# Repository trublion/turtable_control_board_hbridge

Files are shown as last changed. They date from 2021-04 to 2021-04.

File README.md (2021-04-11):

## Description

HW control board for turntable. Controls a DC motor with a H-bridge, reads an analog audio signal envelope, dual-PCB design.

## Links (datasheets and documentation)

[IEC plug](https://www.schurter.com/en/datasheet/typ_6765.pdf)  
[Potentiometer RK09L](https://tech.alpsalpine.com/prod/e/pdf/potentiometer/rotarypotentiometers/rk09l/rk09l.pdf)  
[Neutrik combo](https://www.neutrik.com/en/product/nj3fp6c.pdf)  
[74HCT4066](https://assets.nexperia.com/documents/data-sheet/74HC_HCT4066.pdf)  
[Shunt resistors](https://www.te.com/commerce/DocumentDelivery/DDEController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)  
[BAS21 small signal diode](https://www.vishay.com/docs/85540/bas19.pdf)  
[Zener diodes](https://assets.nexperia.com/documents/data-sheet/BZX84_SER.pdf)  
[Electrolytic capacitors](https://industrial.panasonic.com/cdbs/www-data/pdf/RDE0000/ABA0000C1181.pdf)  
[LM358 comparator](https://www.ti.com/lit/ds/symlink/lm158-n.pdf)  
[LM833 operational amplifier](https://www.ti.com/lit/ds/symlink/lm833-n.pdf)  
[LM2674 DCDC controller](https://www.ti.com/lit/ds/symlink/lm2674.pdf)  
[MBRS3100T3G Schottky power diode](https://www.onsemi.com/pdf/datasheet/mbrs3100t3-d.pdf)  
[RS2 power diode](https://www.semiee.com/file/ELMX/MULTICOMP-RS2A.pdf)  
[Power inductor](https://www.bourns.com/docs/Product-Datasheets/SRR0735A.pdf)

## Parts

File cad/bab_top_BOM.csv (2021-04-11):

Source: | C:\Users\Florian\Documents\dev\trublion\bab leo maurel\v2\cad\bab_top.sch
Date: | 11/04/2021 16:08:11
Tool: | Eeschema (5.1.9)-1
Generator: | E:\dev\KiCad\bin\scripting\plugins/bom_csv_grouped_by_value.py
Component Count: | 106
Individual Components:
Item | Qty | Reference(s) | Value | LibPart | Footprint | Datasheet
 |  | C101 | 100n | Device:C | Capacitors_SMD:C_0805_HandSoldering
 |  | C102 | 100n | Device:C | Capacitors_SMD:C_0805_HandSoldering
 |  | C201 | 1u | Device:C | Capacitors_SMD:C_2220_HandSoldering
 |  | C202 | 100p | Device:C | Capacitors_SMD:C_0805_HandSoldering
 |  | C203 | 47u | Device:C | Capacitors_SMD:c_elec_6.3x5.8
 |  | C204 | 47u | Device:C | Capacitors_SMD:c_elec_6.3x5.8
 |  | C205 | 100p | Device:C | Capacitors_SMD:C_0805_HandSoldering
 |  | C206 | 47u | Device:C | Capacitors_SMD:c_elec_6.3x5.8
 |  | C207 | 6.8u | Device:C | Capacitors_SMD:c_elec_5x5.7
 |  | C208 | 100n | Device:C | Capacitors_SMD:C_0805_HandSoldering
 |  | C209 | 10u | Device:C | Capacitors_SMD:c_elec_6.3x5.8
 |  | C303 | 100u | Device:CP | Capacitors_SMD:c_elec_6.3x7.7
 |  | C304 | 100n | Device:C | Capacitors_SMD:C_0805_HandSoldering
 |  | C305 | 10n | Device:C | Capacitors_SMD:C_0805_HandSoldering
 |  | C306 | 100u | Device:CP | Capacitors_SMD:c_elec_6.3x7.7
 |  | C307 | 100n | Device:C | Capacitors_SMD:C_0805_HandSoldering
 |  | C401 | 100u | Device:CP | Capacitors_SMD:c_elec_6.3x7.7
 |  | C402 | 470p | Device:C | Capacitors_SMD:C_0805_HandSoldering
 |  | C403 | 10n | Device:C | Capacitors_SMD:C_0805_HandSoldering
 |  | C404 | 100u | Device:CP | Capacitors_SMD:c_elec_6.3x7.7
 |  | C405 | 10u | Device:CP | Capacitors_SMD:c_elec_6.3x5.8
 |  | C406 | 220n | Device:C | Capacitors_SMD:C_0805_HandSoldering
 |  | C407 | 470u | Device:CP | bab_footprint:c_elec_16x16.8
 |  | C408 | 100n | Device:C | Capacitors_SMD:C_0805_HandSoldering
 |  | C409 | 15n | Device:C | Capacitors_SMD:C_0805_HandSoldering
 |  | C410 | 15n | Device:C | Capacitors_SMD:C_0805_HandSoldering
 |  | C411 | 4.7n | Device:C | Capacitors_SMD:C_0805_HandSoldering
 |  | C412 | 100n | Device:C | Capacitors_SMD:C_0805_HandSoldering
 |  | D101 | BAS21 | bab:BAS21 | TO_SOT_Packages_SMD:SOT-23
 |  | D201 | BAS21 | bab:BAS21 | TO_SOT_Packages_SMD:SOT-23
 |  | D202 | BAS21 | bab:BAS21 | TO_SOT_Packages_SMD:SOT-23
 |  | D301 | MBRS3100T3G | Device:D_Schottky | Diodes_SMD:DO-214AB
 |  | D302 | MBRS3100T3G | Device:D_Schottky | Diodes_SMD:DO-214AB
 |  | D303 | MBRS3100T3G | Device:D_Schottky | Diodes_SMD:DO-214AB
 |  | D401 | BZX84C5V1 | bab:BZX84C5V1 | TO_SOT_Packages_SMD:SOT-23
 |  | D402 | BAS21 | bab:BAS21 | TO_SOT_Packages_SMD:SOT-23
 |  | D403 | BAS21 | bab:BAS21 | TO_SOT_Packages_SMD:SOT-23
 |  | D404 | RS2M | Device:D | bab_footprint:DO-214AA_Handsoldering
 |  | D405 | RS2M | Device:D | bab_footprint:DO-214AA_Handsoldering
 |  | D406 | BZX84C5V1 | bab:BZX84C5V1 | TO_SOT_Packages_SMD:SOT-23
 |  | K101 | XLR3 | bab_top-rescue:XLR3 | Pin_Headers:Pin_Header_Straight_1x03
 |  | K102 | XLR3 | bab_top-rescue:XLR3 | Pin_Headers:Pin_Header_Straight_1x03
 |  | L301 | 100u | bab_top-rescue:INDUCTOR | Choke_SMD:Choke_SMD_7.3x7.3_H3.5
 |  | P2 | CONN_01X02 | bab_top-rescue:CONN_01X02 | Pin_Headers:Pin_Header_Straight_1x02
 |  | P3 | CONN_01X02 | bab_top-rescue:CONN_01X02 | Pin_Headers:Pin_Header_Straight_1x02
 |  | P4 | CONN_01X02 | bab_top-rescue:CONN_01X02 | Pin_Headers:Pin_Header_Straight_1x02
 |  | P5 | CONN_01X03 | bab_top-rescue:CONN_01X03 | Pin_Headers:Pin_Header_Straight_1x03
 |  | P6 | CONN_01X03 | bab_top-rescue:CONN_01X03 | Pin_Headers:Pin_Header_Straight_1x03
 |  | P101 | CONN_01X02 | bab_top-rescue:CONN_01X02 | Connect:bornier2
 |  | P102 | CONN_01X02 | bab_top-rescue:CONN_01X02 | Connect:bornier2
 |  | P103 | Nulceo_F303K8_CONN | bab:Nulceo_F303K8_CONN | bab_footprint:Nucleo_F303K8_CONN
 |  | P104 | CONN_01X03 | bab_top-rescue:CONN_01X03 | Pin_Headers:Pin_Header_Straight_1x03
 |  | P105 | CONN_01X03 | bab_top-rescue:CONN_01X03 | Pin_Headers:Pin_Header_Straight_1x03
 |  | P106 | CONN_01X02 | bab_top-rescue:CONN_01X02 | Connect:bornier2
 |  | P107 | CONN_01X02 | bab_top-rescue:CONN_01X02 | Connect:bornier2
 |  | P108 | CONN_01X03 | bab_top-rescue:CONN_01X03 | Pin_Headers:Pin_Header_Straight_1x03
 |  | P109 | CONN_01X03 | bab_top-rescue:CONN_01X03 | Pin_Headers:Pin_Header_Straight_1x03
 |  | Q1 | DTC123Y | bab_top-rescue:DTC123Y | TO_SOT_Packages_SMD:SOT-23_Handsoldering
 |  | Q401 | DTC123Y | bab_top-rescue:DTC123Y | TO_SOT_Packages_SMD:SOT-23
 |  | Q402 | DTC123Y | bab_top-rescue:DTC123Y | TO_SOT_Packages_SMD:SOT-23
 |  | R1 | 1k | Device:R | Resistors_SMD:R_0805_HandSoldering
 |  | R2 | 1k | Device:R | Resistors_SMD:R_0805_HandSoldering
 |  | R103 | 33k | Device:R | Capacitors_SMD:C_0805_HandSoldering
 |  | R104 | 4.7k | Device:R | Capacitors_SMD:C_0805_HandSoldering
 |  | R105 | 10k | Device:R | Capacitors_SMD:C_0805_HandSoldering
 |  | R106 | 0 | Device:R | Capacitors_SMD:C_0805_HandSoldering
 |  | R201 | 1k | Device:R | Capacitors_SMD:C_0805_HandSoldering
 |  | R202 | 1M | Device:R | Capacitors_SMD:C_0805_HandSoldering
 |  | R203 | 33k | Device:R | Capacitors_SMD:C_0805_HandSoldering
 |  | R204 | 33k | Device:R | Capacitors_SMD:C_0805_HandSoldering
 |  | R205 | 1k | Device:R | Capacitors_SMD:C_0805_HandSoldering
 |  | R206 | 100 | Device:R | Capacitors_SMD:C_0805_HandSoldering
 |  | R207 | 75k | Device:R | Capacitors_SMD:C_0805_HandSoldering
 |  | R208 | 10k | Device:R | Capacitors_SMD:C_0805_HandSoldering
 |  | R209 | 33k | Device:R | Capacitors_SMD:C_0805_HandSoldering
 |  | R210 | 33k | Device:R | Capacitors_SMD:C_0805_HandSoldering
 |  | R211 | 33k | Device:R | Capacitors_SMD:C_0805_HandSoldering
 |  | R212 | 33k | Device:R | Capacitors_SMD:C_0805_HandSoldering
 |  | R213 | 33k | Device:R | Capacitors_SMD:C_0805_HandSoldering
 |  | R214 | 10k | Device:R | Capacitors_SMD:C_0805_HandSoldering
 |  | R401 | 4k7 | Device:R | Capacitors_SMD:C_0805_HandSoldering
 |  | R402 | 1k | Device:R | Capacitors_SMD:C_0805_HandSoldering
 |  | R404 | 1k | Device:R | Capacitors_SMD:C_0805_HandSoldering
 |  | R405 | 10k | Device:R | Capacitors_SMD:C_0805_HandSoldering
 |  | R406 | 0 | Device:R | Capacitors_SMD:C_0805_HandSoldering
 |  | R407 | 0 | Device:R | Capacitors_SMD:C_0805_HandSoldering
 |  | R408 | 10k | Device:R | Capacitors_SMD:C_0805_HandSoldering
 |  | R409 | 0 | Device:R | Capacitors_SMD:C_0805_HandSoldering
 |  | R410 | 0 | Device:R | Capacitors_SMD:C_0805_HandSoldering
 |  | R411 | 0 | Device:R | Capacitors_SMD:C_0805_HandSoldering
 |  | R412 | 0 | Device:R | Capacitors_SMD:C_0805_HandSoldering
 |  | R413 | 0 | Device:R | Capacitors_SMD:C_0805_HandSoldering
 |  | R414 | 24 | Device:R | bab_footprint:C_3522_HandSoldering
 |  | RV101 | 10k | bab_top-rescue:POT | Pin_Headers:Pin_Header_Straight_1x03
 |  | RV201 | 100k | bab_top-rescue:POT | Pin_Headers:Pin_Header_Straight_1x03
 |  | RV202 | 10k | bab_top-rescue:POT | Pin_Headers:Pin_Header_Straight_1x03
 |  | RV203 | 1k | bab_top-rescue:POT | Pin_Headers:Pin_Header_Straight_1x03
 |  | RV204 | 1M | bab_top-rescue:POT | Pin_Headers:Pin_Header_Straight_1x03
 |  | RV205 | 100k | bab_top-rescue:POT | Pin_Headers:Pin_Header_Straight_1x03
 |  | SW401 | SWITCH_INV | bab_top-rescue:SWITCH_INV | Pin_Headers:Pin_Header_Straight_1x03
 |  | U201 | LM833 | bab:LM833 | Housings_SOIC:SOIC-8_3.9x4.9mm_Pitch1.27mm
 |  | U202 | LM358 | bab_top-rescue:LM358-RESCUE-bab_top | Housings_SOIC:SOIC-8_3.9x4.9mm_Pitch1.27mm
 |  | U301 | LM2674 | bab:LM2674 | Housings_SOIC:SOIC-8_3.9x4.9mm_Pitch1.27mm
 |  | U401 | LM7812CT | bab_top-rescue:LM7812CT | Power_Integrations:TO-220
 |  | U402 | LM555N | bab_top-rescue:LM555N-RESCUE-bab_top | Housings_SOIC:SOIC-8_3.9x4.9mm_Pitch1.27mm
 |  | U403 | L6203 | bab:L6203 | bab_footprint:Multiwatt_11_Vertical | ~
Collated Components:
Item | Qty | Reference(s) | Value | LibPart | Footprint | Datasheet
1 | 7 | C101, C102, C208, C304, C307, C408, C412 | 100n | Device:C | Capacitors_SMD:C_0805_HandSoldering
2 | 1 | C201 | 1u | Device:C | Capacitors_SMD:C_2220_HandSoldering
3 | 2 | C202, C205 | 100p | Device:C | Capacitors_SMD:C_0805_HandSoldering
4 | 3 | C203, C204, C206 | 47u | Device:C | Capacitors_SMD:c_elec_6.3x5.8
5 | 1 | C207 | 6.8u | Device:C | Capacitors_SMD:c_elec_5x5.7
6 | 1 | C209 | 10u | Device:C | Capacitors_SMD:c_elec_6.3x5.8
7 | 4 | C303, C306, C401, C404 | 100u | Device:CP | Capacitors_SMD:c_elec_6.3x7.7
8 | 2 | C305, C403 | 10n | Device:C | Capacitors_SMD:C_0805_HandSoldering
9 | 1 | C402 | 470p | Device:C | Capacitors_SMD:C_0805_HandSoldering
10 | 1 | C405 | 10u | Device:CP | Capacitors_SMD:c_elec_6.3x5.8
11 | 1 | C406 | 220n | Device:C | Capacitors_SMD:C_0805_HandSoldering
12 | 1 | C407 | 470u | Device:CP | bab_footprint:c_elec_16x16.8
13 | 2 | C409, C410 | 15n | Device:C | Capacitors_SMD:C_0805_HandSoldering
14 | 1 | C411 | 4.7n | Device:C | Capacitors_SMD:C_0805_HandSoldering
15 | 5 | D101, D201, D202, D402, D403 | BAS21 | bab:BAS21 | TO_SOT_Packages_SMD:SOT-23
16 | 3 | D301, D302, D303 | MBRS3100T3G | Device:D_Schottky | Diodes_SMD:DO-214AB
17 | 2 | D401, D406 | BZX84C5V1 | bab:BZX84C5V1 | TO_SOT_Packages_SMD:SOT-23
18 | 2 | D404, D405 | RS2M | Device:D | bab_footprint:DO-214AA_Handsoldering
19 | 2 | K101, K102 | XLR3 | bab_top-rescue:XLR3 | Pin_Headers:Pin_Header_Straight_1x03
20 | 1 | L301 | 100u | bab_top-rescue:INDUCTOR | Choke_SMD:Choke_SMD_7.3x7.3_H3.5
21 | 3 | P2, P3, P4 | CONN_01X02 | bab_top-rescue:CONN_01X02 | Pin_Headers:Pin_Header_Straight_1x02
22 | 6 | P5, P6, P104, P105, P108, P109 | CONN_01X03 | bab_top-rescue:CONN_01X03 | Pin_Headers:Pin_Header_Straight_1x03
23 | 4 | P101, P102, P106, P107 | CONN_01X02 | bab_top-rescue:CONN_01X02 | Connect:bornier2
24 | 1 | P103 | Nulceo_F303K8_CONN | bab:Nulceo_F303K8_CONN | bab_footprint:Nucleo_F303K8_CONN
25 | 1 | Q1 | DTC123Y | bab_top-rescue:DTC123Y | TO_SOT_Packages_SMD:SOT-23_Handsoldering
26 | 2 | Q401, Q402 | DTC123Y | bab_top-rescue:DTC123Y | TO_SOT_Packages_SMD:SOT-23
27 | 2 | R1, R2 | 1k | Device:R | Resistors_SMD:R_0805_HandSoldering
28 | 8 | R103, R203, R204, R209, R210, R211, R212, R213 | 33k | Device:R | Capacitors_SMD:C_0805_HandSoldering
29 | 1 | R104 | 4.7k | Device:R | Capacitors_SMD:C_0805_HandSoldering
30 | 5 | R105, R208, R214, R405, R408 | 10k | Device:R | Capacitors_SMD:C_0805_HandSoldering
31 | 8 | R106, R406, R407, R409, R410, R411, R412, R413 | 0 | Device:R | Capacitors_SMD:C_0805_HandSoldering
32 | 4 | R201, R205, R402, R404 | 1k | Device:R | Capacitors_SMD:C_0805_HandSoldering
33 | 1 | R202 | 1M | Device:R | Capacitors_SMD:C_0805_HandSoldering
34 | 1 | R206 | 100 | Device:R | Capacitors_SMD:C_0805_HandSoldering
35 | 1 | R207 | 75k | Device:R | Capacitors_SMD:C_0805_HandSoldering
36 | 1 | R401 | 4k7 | Device:R | Capacitors_SMD:C_0805_HandSoldering
37 | 1 | R414 | 24 | Device:R | bab_footprint:C_3522_HandSoldering
38 | 2 | RV101, RV202 | 10k | bab_top-rescue:POT | Pin_Headers:Pin_Header_Straight_1x03
39 | 2 | RV201, RV205 | 100k | bab_top-rescue:POT | Pin_Headers:Pin_Header_Straight_1x03
40 | 1 | RV203 | 1k | bab_top-rescue:POT | Pin_Headers:Pin_Header_Straight_1x03
41 | 1 | RV204 | 1M | bab_top-rescue:POT | Pin_Headers:Pin_Header_Straight_1x03
42 | 1 | SW401 | SWITCH_INV | bab_top-rescue:SWITCH_INV | Pin_Headers:Pin_Header_Straight_1x03
43 | 1 | U201 | LM833 | bab:LM833 | Housings_SOIC:SOIC-8_3.9x4.9mm_Pitch1.27mm
44 | 1 | U202 | LM358 | bab_top-rescue:LM358-RESCUE-bab_top | Housings_SOIC:SOIC-8_3.9x4.9mm_Pitch1.27mm
45 | 1 | U301 | LM2674 | bab:LM2674 | Housings_SOIC:SOIC-8_3.9x4.9mm_Pitch1.27mm
46 | 1 | U401 | LM7812CT | bab_top-rescue:LM7812CT | Power_Integrations:TO-220
47 | 1 | U402 | LM555N | bab_top-rescue:LM555N-RESCUE-bab_top | Housings_SOIC:SOIC-8_3.9x4.9mm_Pitch1.27mm
48 | 1 | U403 | L6203 | bab:L6203 | bab_footprint:Multiwatt_11_Vertical | ~

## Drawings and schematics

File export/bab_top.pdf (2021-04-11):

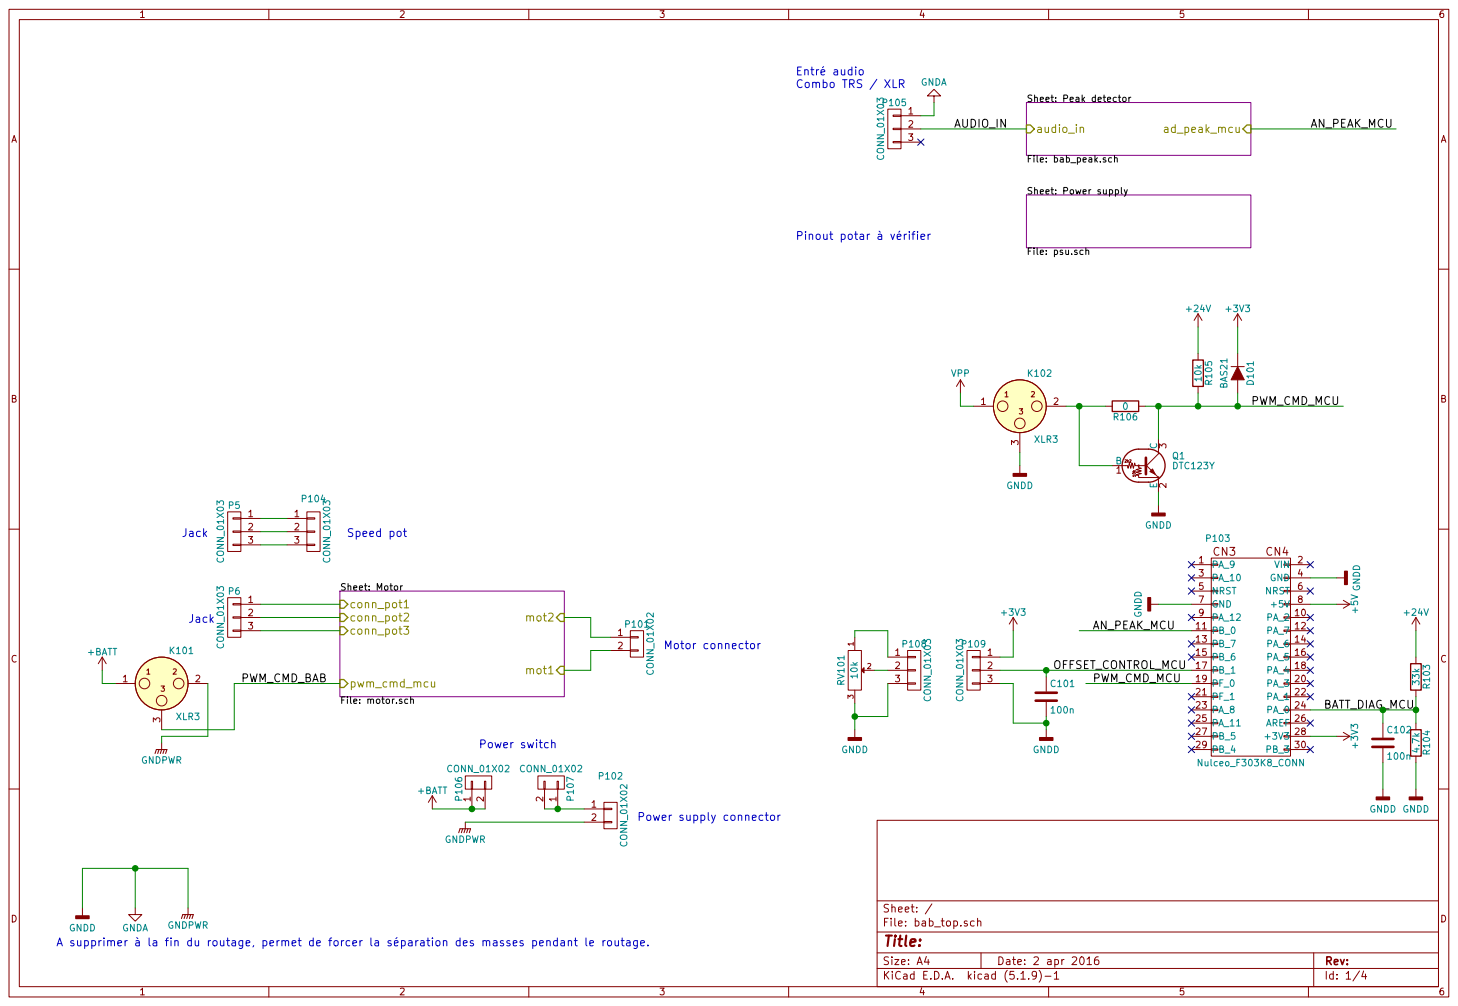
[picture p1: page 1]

File: psu.sch Sheet: Peak detector File: bab_peak.sch

File: bab_top.sch Sheet: / Sheet: Motor File: motor.sch conn_pot1

A supprimer à la fin du routage, permet de forcer la séparation des masses pendant le routage.

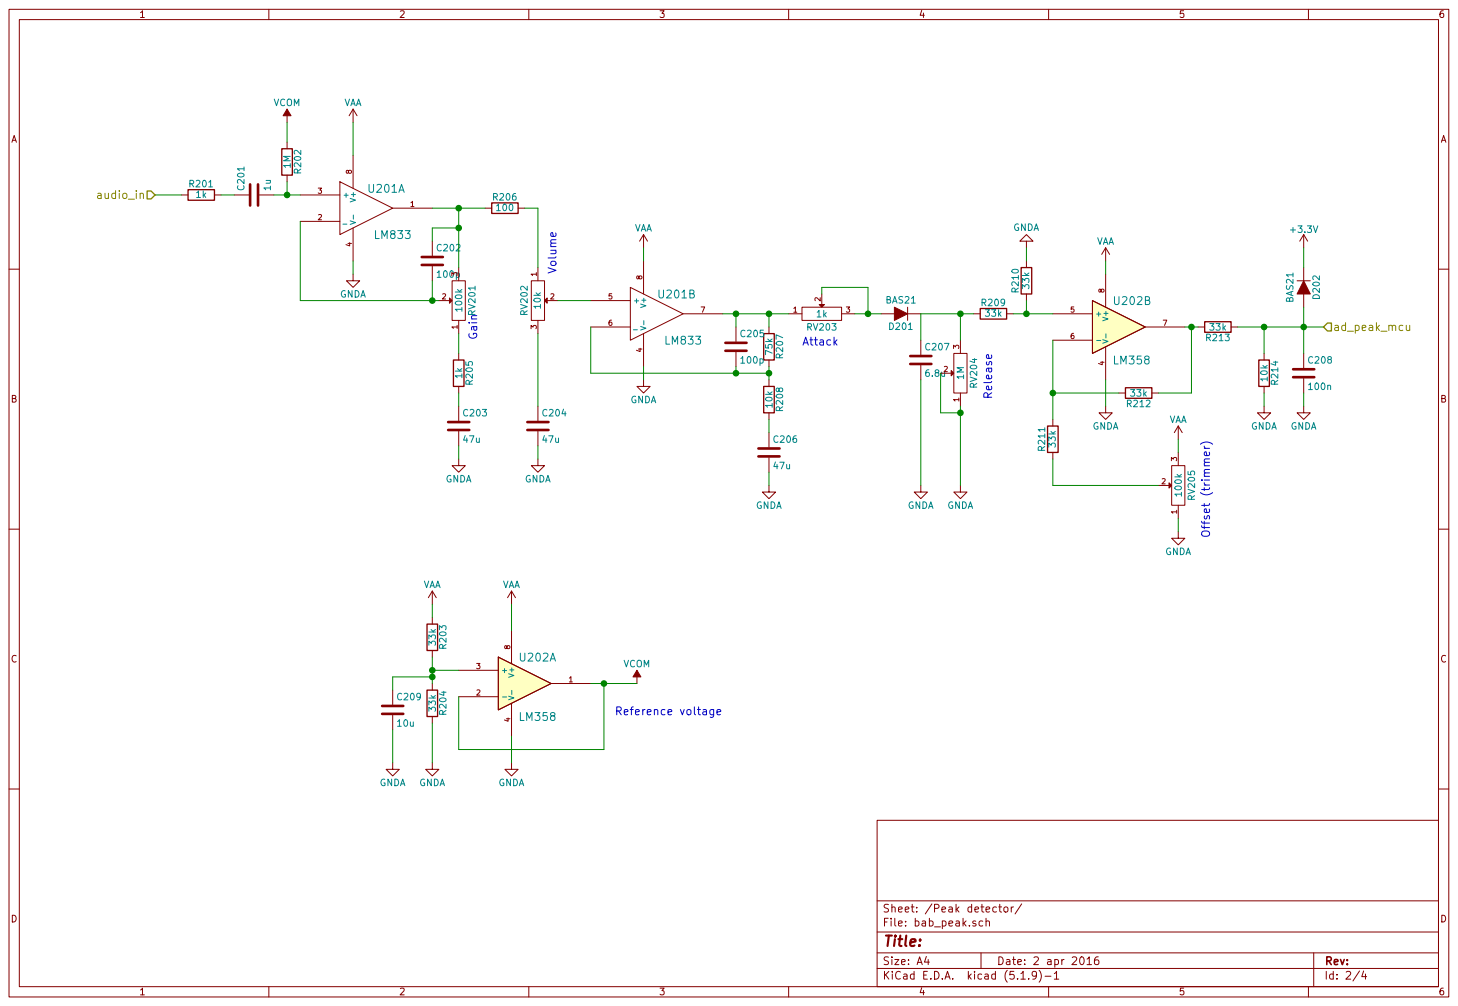
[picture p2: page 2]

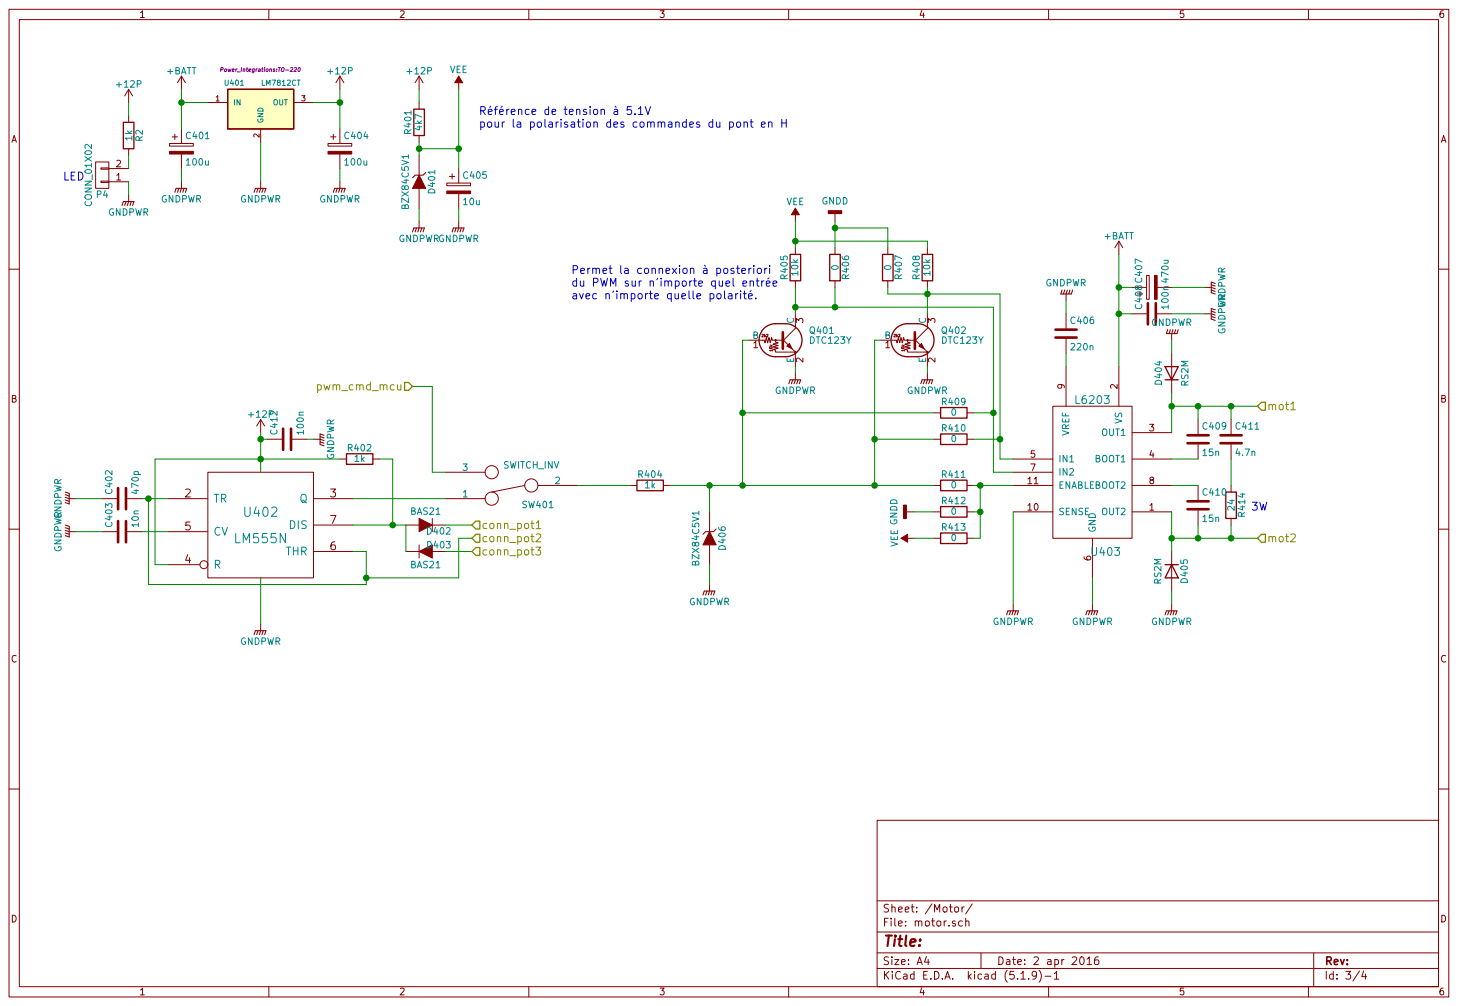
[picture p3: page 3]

Référence de tension à 5.1V
pour la polarisation des commandes du pont en H

avec n'importe quelle polarité. LED

Permet la connexion à posteriori
du PWM sur n'importe quel entrée

Id: 3/4 Title: File: motor.sch Sheet: /Motor/ GNDPWR

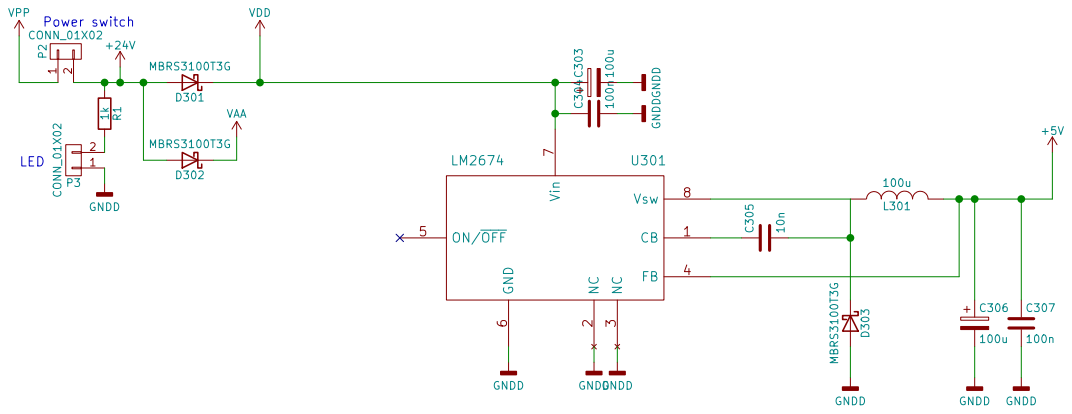
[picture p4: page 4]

3 FB 4 ON/OFF 5 GND

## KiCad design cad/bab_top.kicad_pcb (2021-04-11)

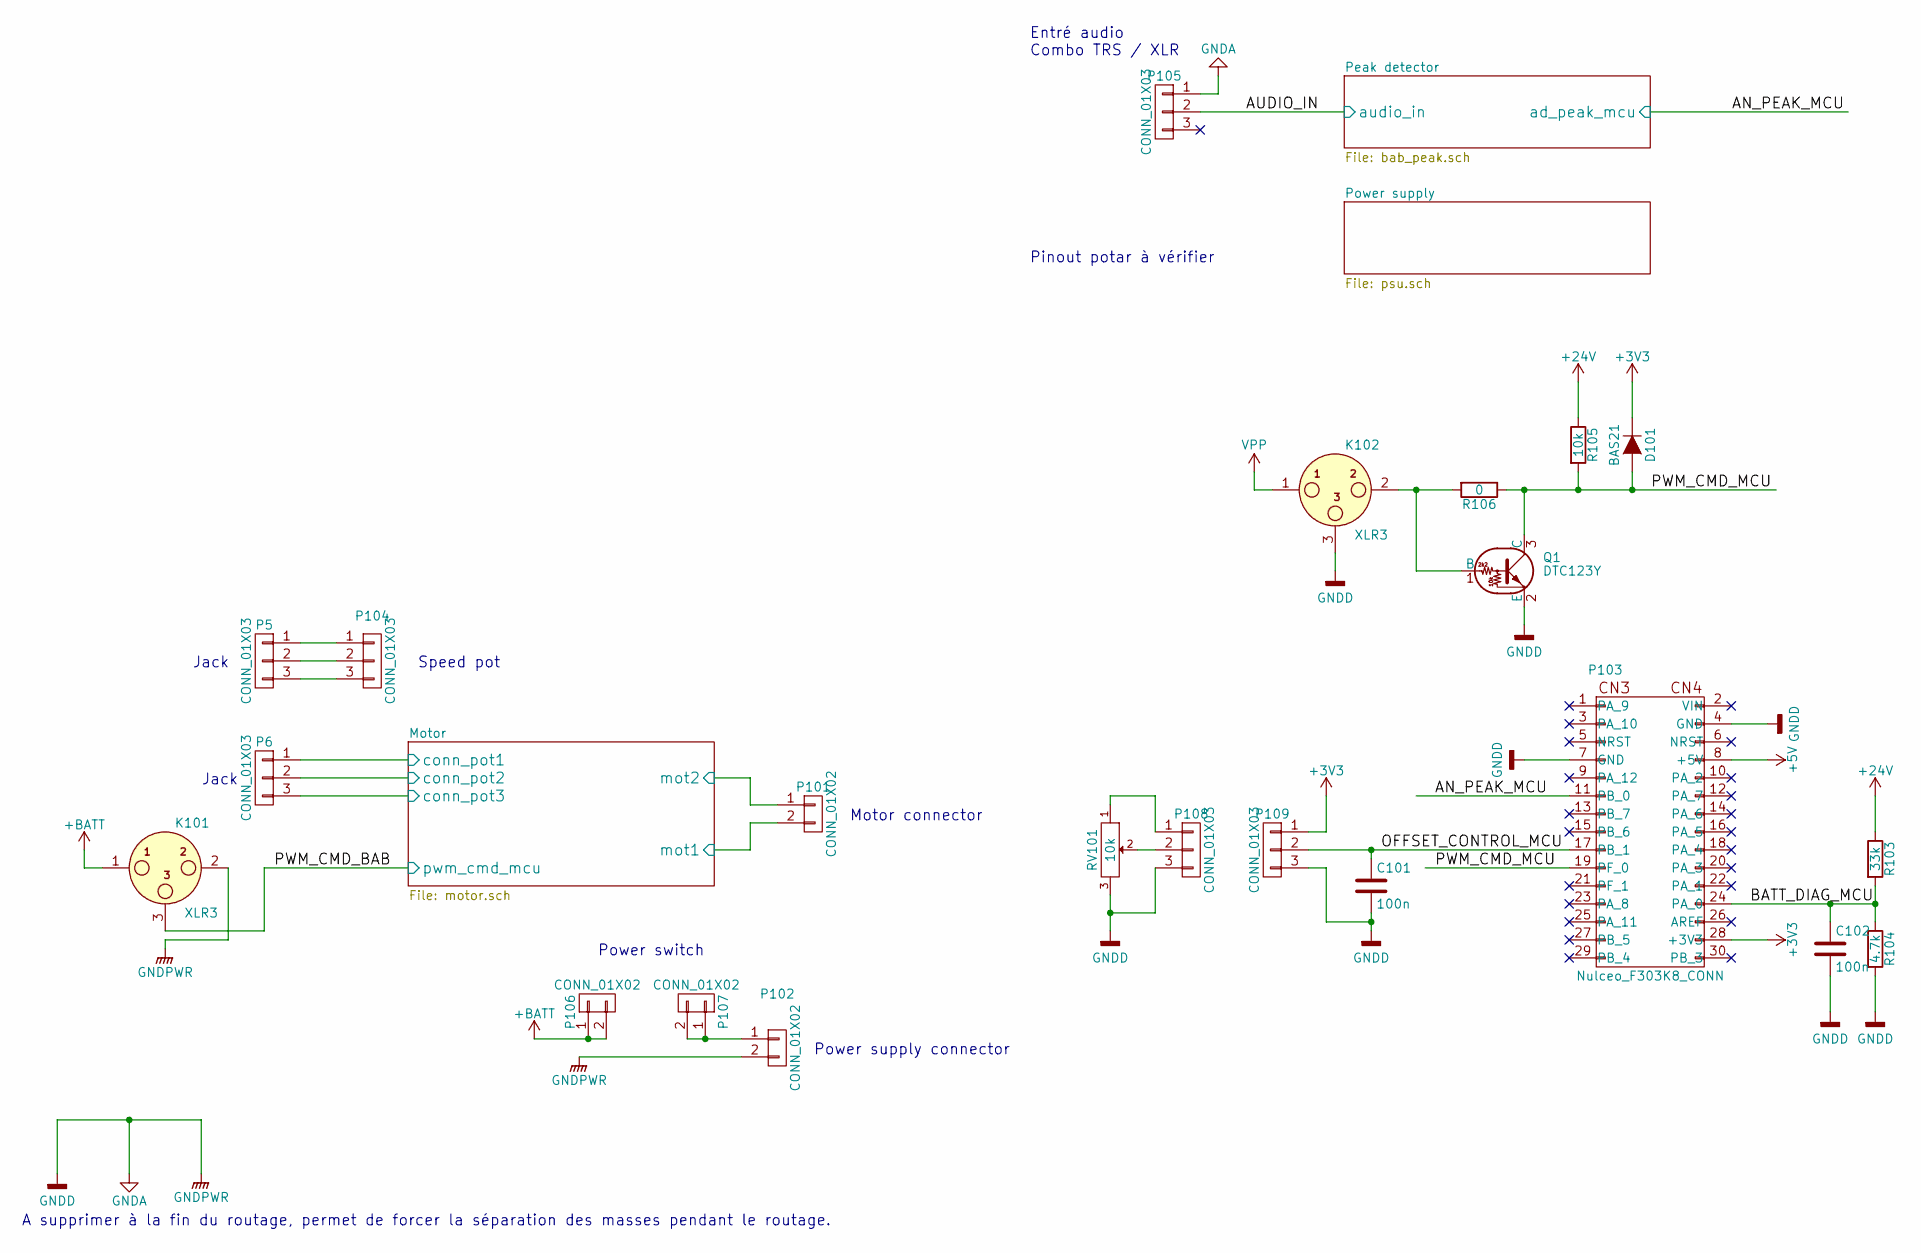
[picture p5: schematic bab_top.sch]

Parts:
C101, C102: 100n; C_0805_HandSoldering
D101: BAS21; SOT-23
K101, K102: XLR3; Pin_Header_Straight_1x03
P5, P6, P104, P105, P108, P109: CONN_01X03; Pin_Header_Straight_1x03
P101, P102, P106, P107: CONN_01X02; bornier2
P103: Nulceo_F303K8_CONN; Nucleo_F303K8_CONN
Q1: DTC123Y; SOT-23_Handsoldering
R103: 33k; C_0805_HandSoldering
R104: 4.7k; C_0805_HandSoldering
R105: 10k; C_0805_HandSoldering
R106: 0; C_0805_HandSoldering
RV101: 10k; Pin_Header_Straight_1x03

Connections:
+5V: P103.8 (+5V); also elsewhere on the board
+24V: R103.1, R105.1; also elsewhere on the board
+BATT: K101.1, P106.1, P106.2; also elsewhere on the board
/BATT_DIAG_MCU: C102.1, P103.24 (PA_0), R103.2, R104.1
/Motor/conn_pot1: P6.1; also elsewhere on the board
/Motor/conn_pot2: P6.2; also elsewhere on the board
/Motor/conn_pot3: P6.3; also elsewhere on the board
/Motor/mot1: P101.2; also elsewhere on the board
/Motor/mot2: P101.1; also elsewhere on the board
/Motor/pwm_cmd_mcu: K101.3; also elsewhere on the board
/OFFSET_CONTROL_MCU: C101.1, P103.17 (PB_1), P109.2
/PWM_CMD_MCU: D101.1 (A), P103.19 (PF_0), Q1.3 (C), R105.2, R106.1
/Peak detector/ad_peak_mcu: P103.11 (PB_0); also elsewhere on the board
/Peak detector/audio_in: P105.2; also elsewhere on the board
GND: C101.2, C102.2, K101.2, K102.3, P102.2, P103.4 (GND), P103.7 (GND), P105.1, P108.3, P109.3, Q1.2 (E), R104.2, RV101.3; also elsewhere on the board
unnamed: K102.2, Q1.1 (B), R106.2
unnamed: P102.1, P107.1, P107.2
unnamed: P5.1, P104.1
unnamed: P5.2, P104.2
unnamed: P5.3, P104.3
unnamed: P108.1, RV101.1
unnamed: P108.2, RV101.2
VPP: K102.1; also elsewhere on the board

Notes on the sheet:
A supprimer à la fin du routage, permet de forcer la séparation des masses pendant le routage.
Pinout potar à vérifier
Entré audio Combo TRS / XLR
Power switch
Jack
Speed pot
Power supply connector
Motor connector

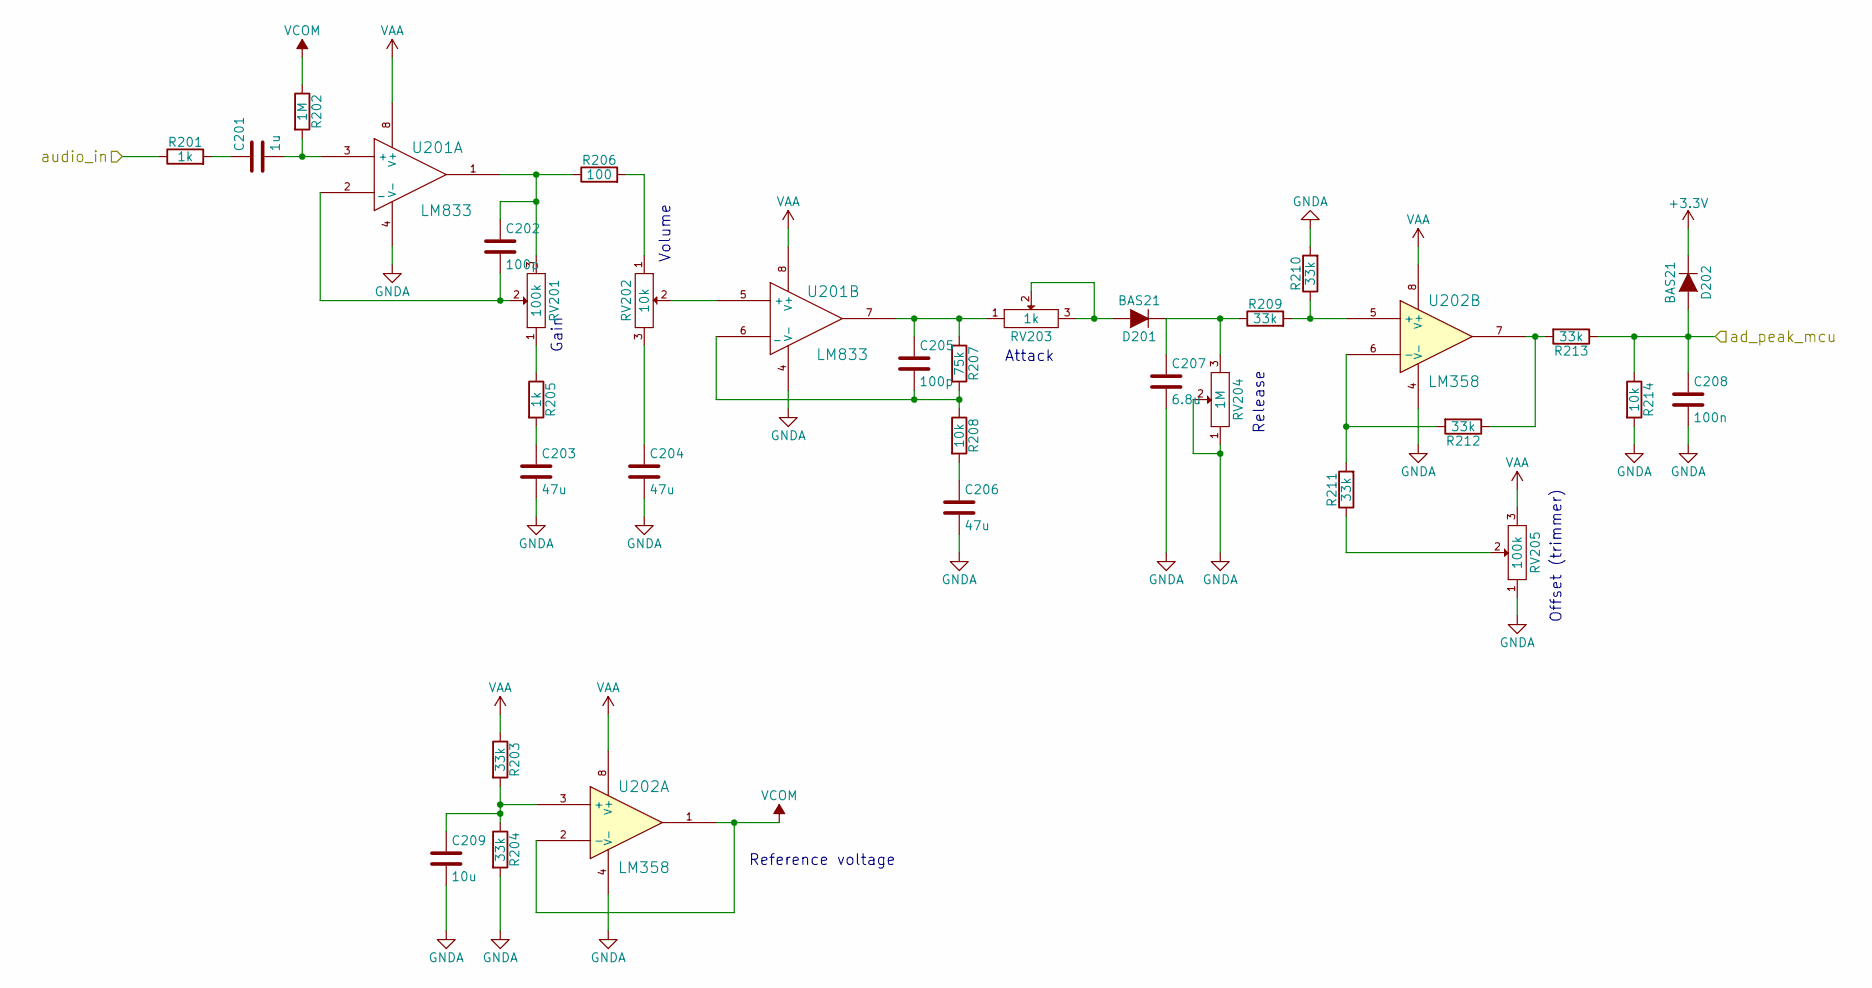
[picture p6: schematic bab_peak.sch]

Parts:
C201: 1u; C_2220_HandSoldering
C202, C205: 100p; C_0805_HandSoldering
C203, C204, C206: 47u; c_elec_6.3x5.8
C207: 6.8u; c_elec_5x5.7
C208: 100n; C_0805_HandSoldering
C209: 10u; c_elec_6.3x5.8
D201, D202: BAS21; SOT-23
R201, R205: 1k; C_0805_HandSoldering
R202: 1M; C_0805_HandSoldering
R203, R204, R209, R210, R211, R212, R213: 33k; C_0805_HandSoldering
R206: 100; C_0805_HandSoldering
R207: 75k; C_0805_HandSoldering
R208, R214: 10k; C_0805_HandSoldering
RV201, RV205: 100k; Pin_Header_Straight_1x03
RV202: 10k; Pin_Header_Straight_1x03
RV203: 1k; Pin_Header_Straight_1x03
RV204: 1M; Pin_Header_Straight_1x03
U201: LM833; SOIC-8_3.9x4.9mm_Pitch1.27mm
U202: LM358; SOIC-8_3.9x4.9mm_Pitch1.27mm

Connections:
/Peak detector/ad_peak_mcu: C208.1, D202.1 (A), R213.1, R214.1; also elsewhere on the board
/Peak detector/audio_in: R201.1; also elsewhere on the board
GND: C203.2, C204.2, C206.2, C207.2, C208.2, C209.2, R204.2, R210.2, R214.2, RV204.1, RV204.2, RV205.1, U201.4 (V-), U202.4 (V-); also elsewhere on the board
unnamed: C201.1, R201.2
unnamed: C201.2, R202.2, U201.3 (+)
unnamed: C202.1, R206.1, RV201.3, U201.1
unnamed: C202.2, RV201.2, U201.2 (_)
unnamed: C203.1, R205.2
unnamed: C204.1, RV202.3
unnamed: C205.1, R207.1, RV203.1, U201.7
unnamed: C205.2, R207.2, R208.1, U201.6 (_)
unnamed: C206.1, R208.2
unnamed: C207.1, D201.3 (K), R209.1, RV204.3
unnamed: C209.1, R203.2, R204.1, U202.3 (+)
unnamed: D201.1 (A), RV203.2, RV203.3
unnamed: R205.1, RV201.1
unnamed: R206.2, RV202.1
unnamed: R209.2, R210.1, U202.5 (+)
unnamed: R211.1, RV205.2
unnamed: R211.2, R212.2, U202.6 (-)
unnamed: R212.1, R213.2, U202.7
unnamed: RV202.2, U201.5 (+)
VAA: R203.1, RV205.3, U201.8 (V+), U202.8 (V+); also elsewhere on the board
VCOM: R202.1, U202.1, U202.2 (-)

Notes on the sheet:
Offset (trimmer)
Release
Attack
Gain
Volume
Reference voltage

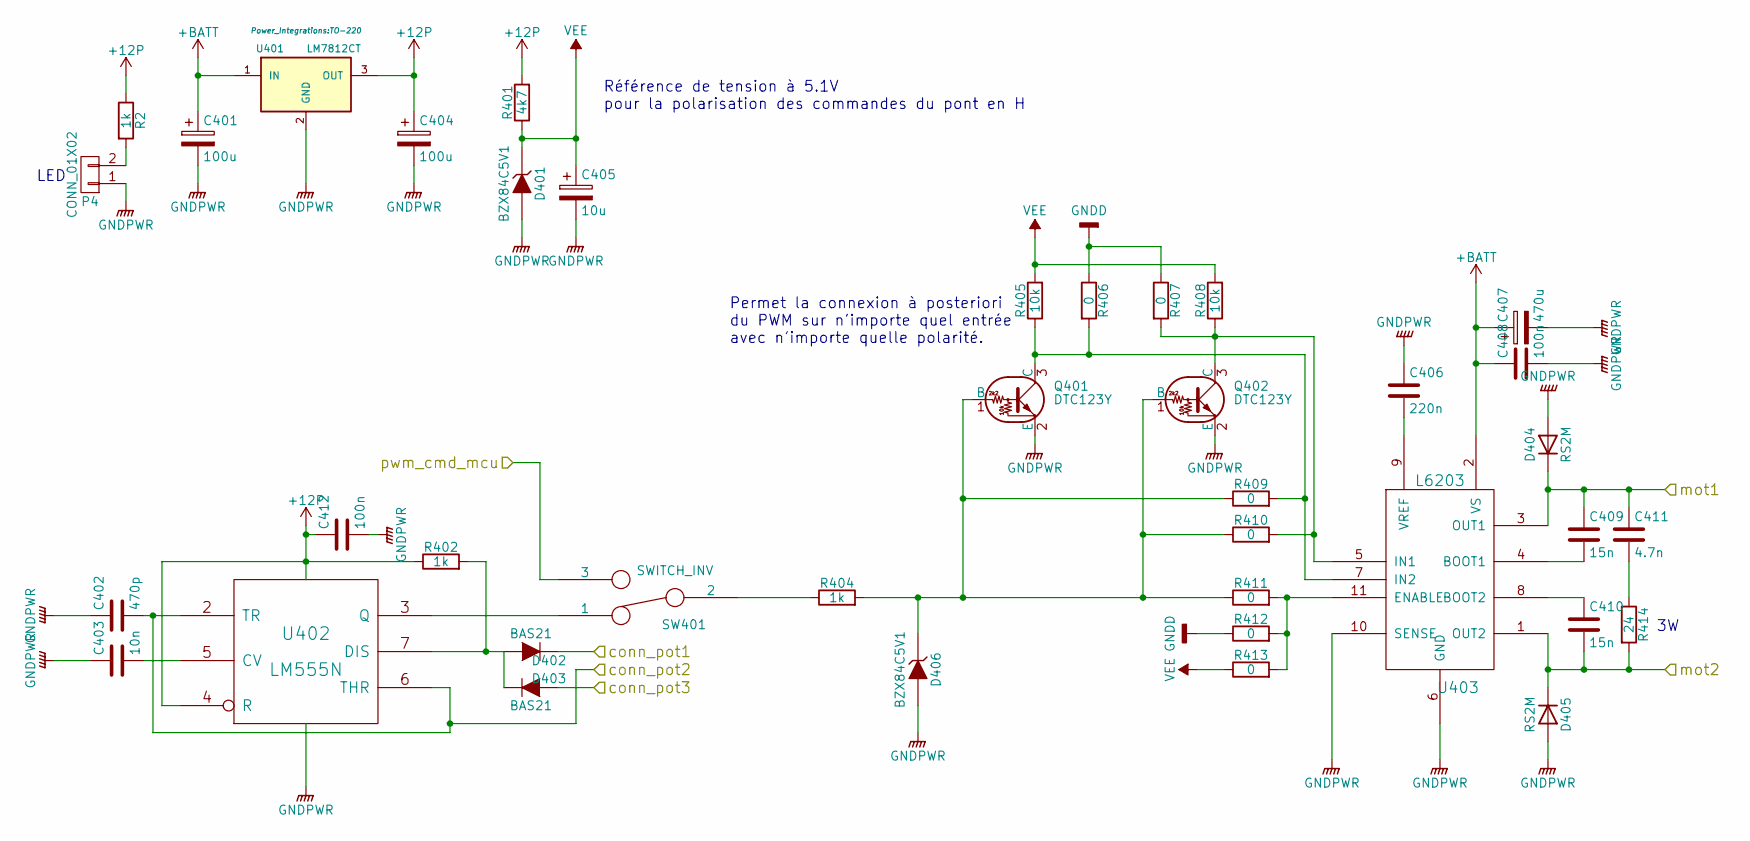
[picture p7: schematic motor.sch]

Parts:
C401, C404: 100u; c_elec_6.3x7.7
C402: 470p; C_0805_HandSoldering
C403: 10n; C_0805_HandSoldering
C405: 10u; c_elec_6.3x5.8
C406: 220n; C_0805_HandSoldering
C407: 470u; c_elec_16x16.8
C408, C412: 100n; C_0805_HandSoldering
C409, C410: 15n; C_0805_HandSoldering
C411: 4.7n; C_0805_HandSoldering
D401, D406: BZX84C5V1; SOT-23
D402, D403: BAS21; SOT-23
D404, D405: RS2M; DO-214AA_Handsoldering
P4: CONN_01X02; Pin_Header_Straight_1x02
Q401, Q402: DTC123Y; SOT-23
R2: 1k; R_0805_HandSoldering
R401: 4k7; C_0805_HandSoldering
R402, R404: 1k; C_0805_HandSoldering
R405, R408: 10k; C_0805_HandSoldering
R406, R407, R409, R410, R411, R412, R413: 0; C_0805_HandSoldering
R414: 24; C_3522_HandSoldering
SW401: SWITCH_INV; Pin_Header_Straight_1x03
U401: LM7812CT; TO-220
U402: LM555N; SOIC-8_3.9x4.9mm_Pitch1.27mm
U403: L6203; Multiwatt_11_Vertical

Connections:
+12P: C404.1, C412.1, R2.1, R401.2, R402.1, U401.3 (OUT), U402.4 (R), U402.8 (VCC)
+BATT: C401.1, C407.1, C408.1, U401.1 (IN), U403.2 (VS); also elsewhere on the board
/Motor/conn_pot1: D402.3 (K); also elsewhere on the board
/Motor/conn_pot2: C402.2, U402.2 (TR), U402.6 (THR); also elsewhere on the board
/Motor/conn_pot3: D403.1 (A); also elsewhere on the board
/Motor/mot1: C409.1, C411.1, D404.1 (K), U403.3 (OUT1); also elsewhere on the board
/Motor/mot2: C410.2, D405.1 (K), R414.2, U403.1 (OUT2); also elsewhere on the board
/Motor/pwm_cmd_mcu: SW401.3; also elsewhere on the board
GND: C401.2, C402.1, C403.1, C404.2, C405.2, C406.1, C407.2, C408.2, C412.2, D401.1 (A), D404.2 (A), D405.2 (A), D406.1 (A), P4.1, Q401.2 (E), Q402.2 (E), R406.1, R407.1, R412.1, U401.2 (GND), U402.1 (GND), U403.6 (GND), U403.10 (SENSE); also elsewhere on the board
unnamed: C403.2, U402.5 (CV)
unnamed: C406.2, U403.9 (VREF)
unnamed: C409.2, U403.4 (BOOT1)
unnamed: C410.1, U403.8 (BOOT2)
unnamed: C411.2, R414.1
unnamed: D402.1 (A), D403.3 (K), R402.2, U402.7 (DIS)
unnamed: D406.3 (K), Q401.1 (B), Q402.1 (B), R404.2, R409.1, R410.1, R411.1
unnamed: P4.2, R2.2
unnamed: Q401.3 (C), R405.1, R406.2, R409.2, U403.7 (IN2)
unnamed: Q402.3 (C), R407.2, R408.1, R410.2, U403.5 (IN1)
unnamed: R404.1, SW401.2
unnamed: R411.2, R412.2, R413.2, U403.11 (ENABLE)
unnamed: SW401.1, U402.3 (Q)
VEE: C405.1, D401.3 (K), R401.1, R405.2, R408.2, R413.1

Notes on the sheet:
Référence de tension à 5.1V pour la polarisation des commandes du pont en H
Permet la connexion à posteriori du PWM sur n'importe quel entrée avec n'importe quelle polarité.
LED

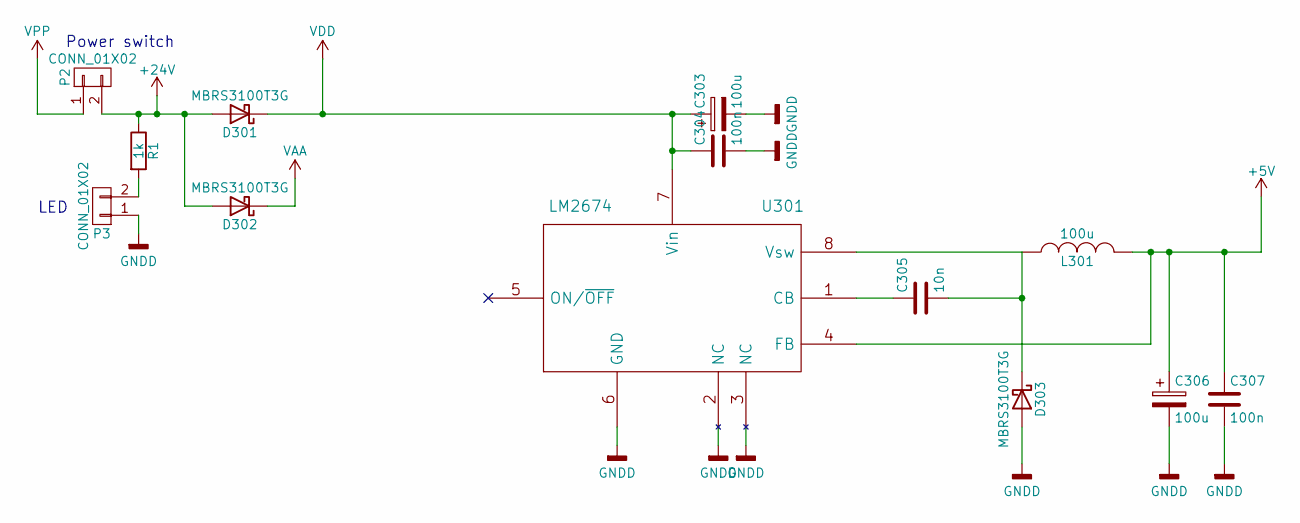
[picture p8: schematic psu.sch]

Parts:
C303, C306: 100u; c_elec_6.3x7.7
C304, C307: 100n; C_0805_HandSoldering
C305: 10n; C_0805_HandSoldering
D301, D302, D303: MBRS3100T3G; DO-214AB
L301: 100u; Choke_SMD_7.3x7.3_H3.5
P2, P3: CONN_01X02; Pin_Header_Straight_1x02
R1: 1k; R_0805_HandSoldering
U301: LM2674; SOIC-8_3.9x4.9mm_Pitch1.27mm

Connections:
+5V: C306.1, C307.1, L301.2, U301.4 (FB); also elsewhere on the board
+24V: D301.2 (A), D302.2 (A), P2.2, R1.1; also elsewhere on the board
GND: C303.2, C304.2, C306.2, C307.2, D303.2 (A), P3.1, U301.2 (NC), U301.3 (NC), U301.6 (GND); also elsewhere on the board
unnamed: C305.1, U301.1 (CB)
unnamed: C305.2, D303.1 (K), L301.1, U301.8 (Vsw)
unnamed: P3.2, R1.2
VAA: D302.1 (K); also elsewhere on the board
VDD: C303.1, C304.1, D301.1 (K), U301.7 (Vin)
VPP: P2.1; also elsewhere on the board

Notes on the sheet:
Power switch
LED

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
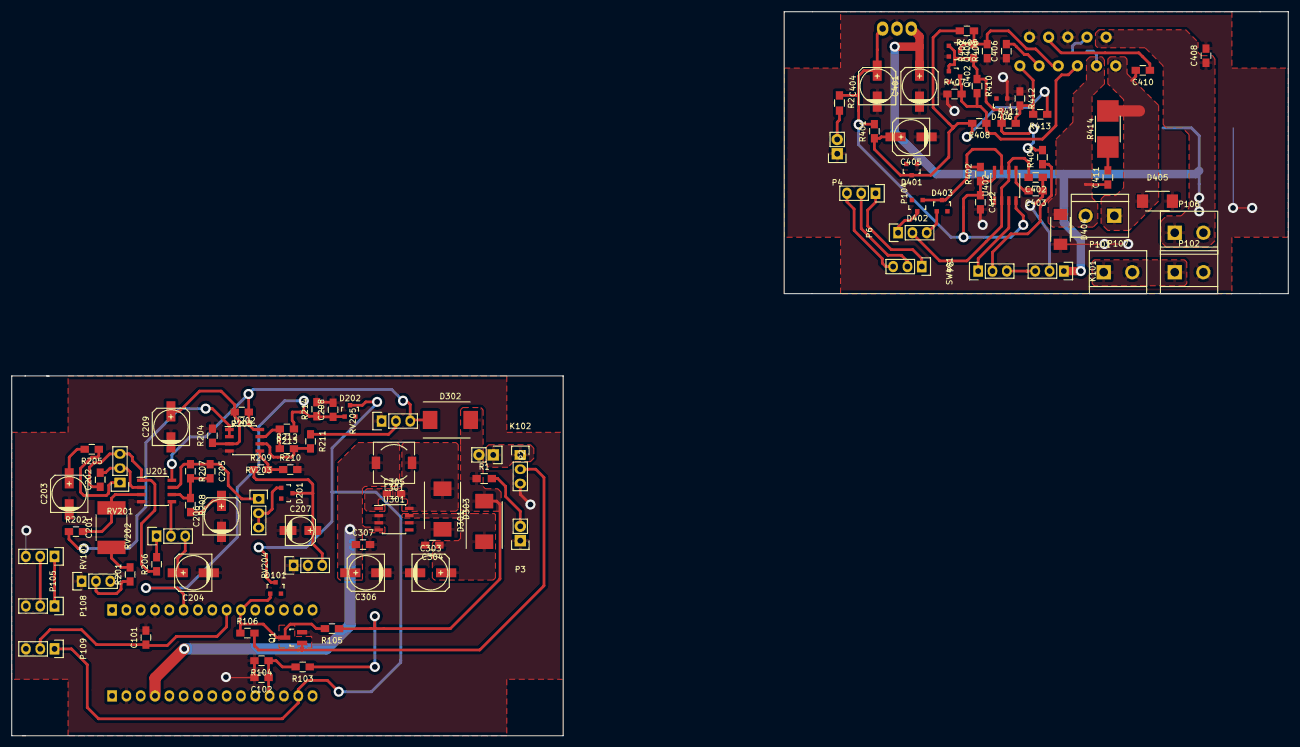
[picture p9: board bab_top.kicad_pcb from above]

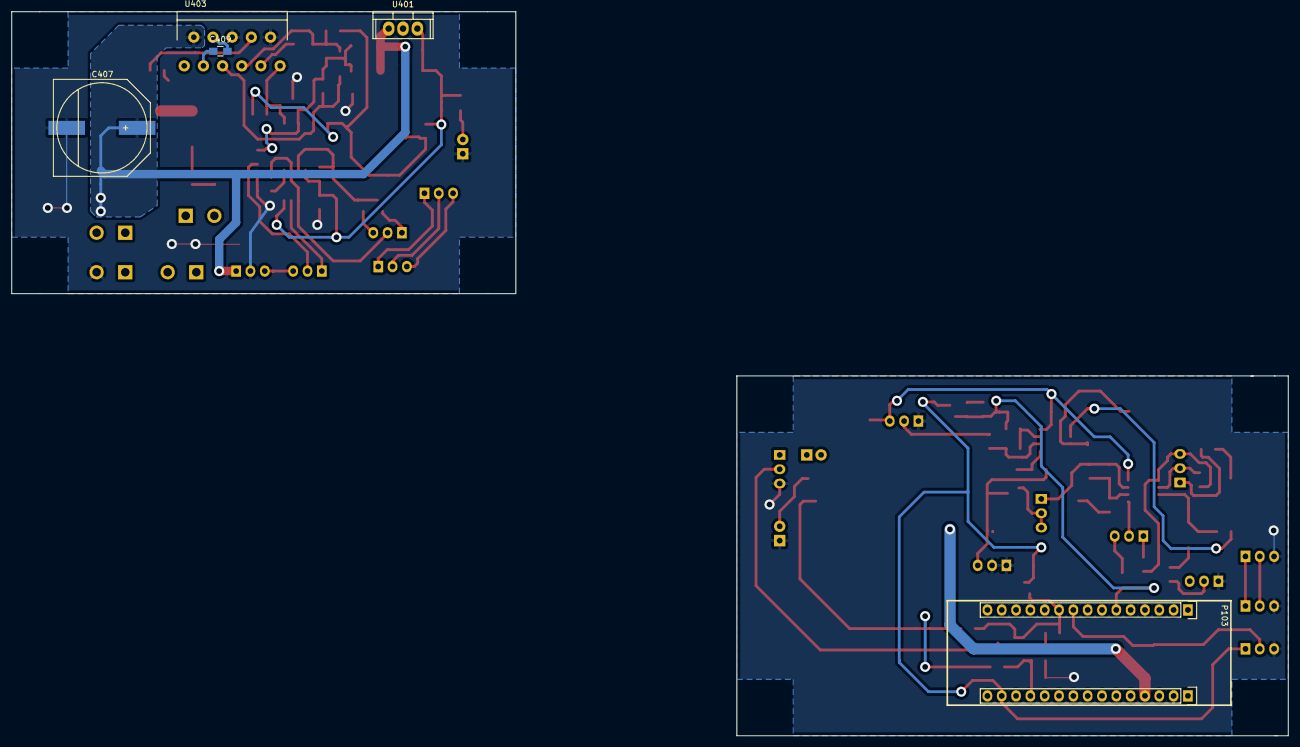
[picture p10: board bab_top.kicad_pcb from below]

Board: 2 copper layers, 226.4 x 128.4 mm, 106 parts (5 on the bottom side), 64 nets.
